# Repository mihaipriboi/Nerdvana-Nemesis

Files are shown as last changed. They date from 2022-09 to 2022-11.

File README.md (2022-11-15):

# Nerdvana Nemesis

### Team: Antonia Onisoru, Teodor Balan, Mihai Priboi
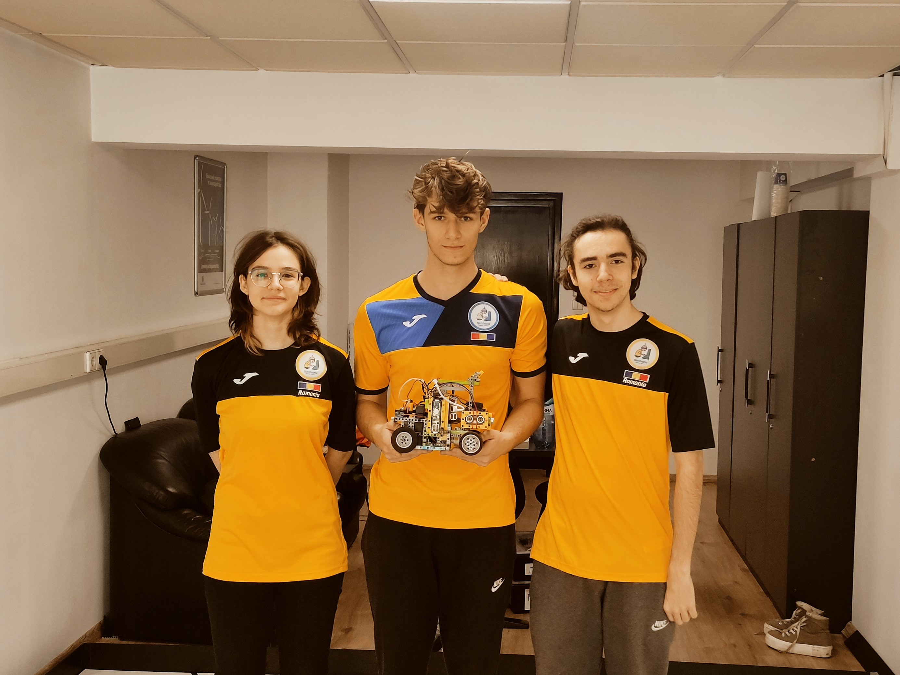
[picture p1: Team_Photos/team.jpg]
Team
  

## Our video of the robot on [Youtube](https://youtu.be/-w9J5_oPF1A)

## Repository content
  - The "Final" folder contains the final code for the final stage
  - The "Qualifing" folder contains the final code for the qualification stage
  - The "Electrical Diagram" folder contains a schematic of the electromechanical representation of the robot
  - The "3D_models" folder contains 3D models for printing the robot
  - The "Robot Photos" folder contains the robot photos required by the regulation
  - The "Team Photos" folder contains the team photos required by the regulation

## Introduction
  We have been participating at WRO for the last couple of years, but 2022 was the first year when, in our country, Romania, Future Engineers was held. When we first started thinking about how to build our robot, we realized that it was not going to be the same as we were used to. 
  
  It was clear to us that lego electronics weren't going to be good enough for what we wanted, so we decided to use Raspberry Pi and Arduino so we could use cameras and other sensors. Since the Arduino is better for sensors, but we could only use a Raspberry Pi for a camera, we decided to use both, in serial communication. As for connecting all the pieces, we still used lego pieces with 3D-printed parts for the non-lego components. In this way, we have a modular robot, easy to modify, so it was simple to try different mechanisms during the year. 

  For the national competition, we came up with the idea of using an Arduino to measure distances with 2 ultrasonic sensors, and a Raspberry pi to identify the cubes with a camera, and also control the drive and steering motors. We have constructed the robot so it has rear-wheel drive with frontal steering.
  
   After we qualified for the international, we started making some changes, such as trying to make the robot faster and more constant. So we added a gyroscope sensor, and an ultrasonic sensor in the front and made the robot smaller. Also, we upgraded from an Arduino Uno to an Arduino Nano Every, because it has more interrupt pins. In addition, we tried changing the drive motor to a micromotor in order to make it faster. Unfortunately, even though it made the robot much faster, we fried the ones we tested. We believe it happened because the robot was too heavy for the motor, causing it to overheat and eventually fry it.

## Photos our robot Paula (**P**retty **A**wesome **U**ltra **L**ow **A**ccurate robot)
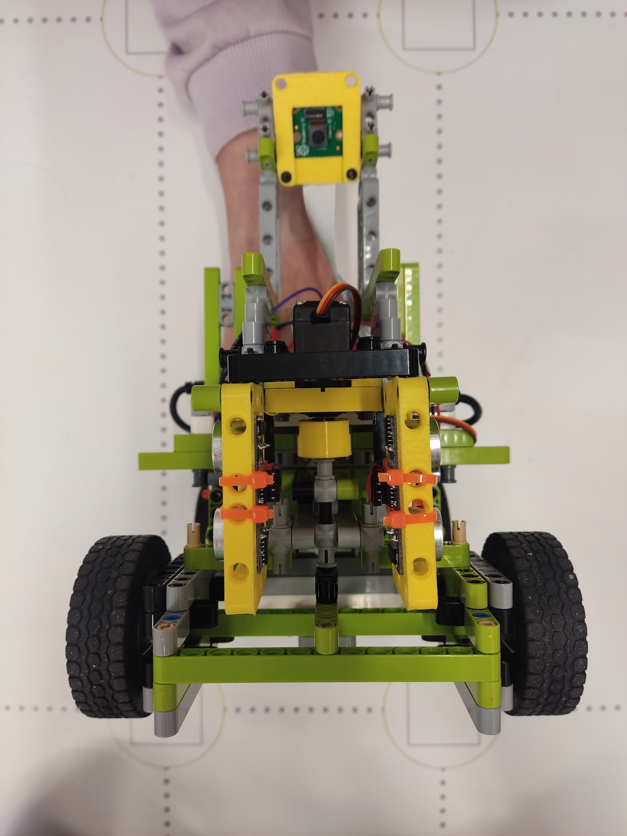
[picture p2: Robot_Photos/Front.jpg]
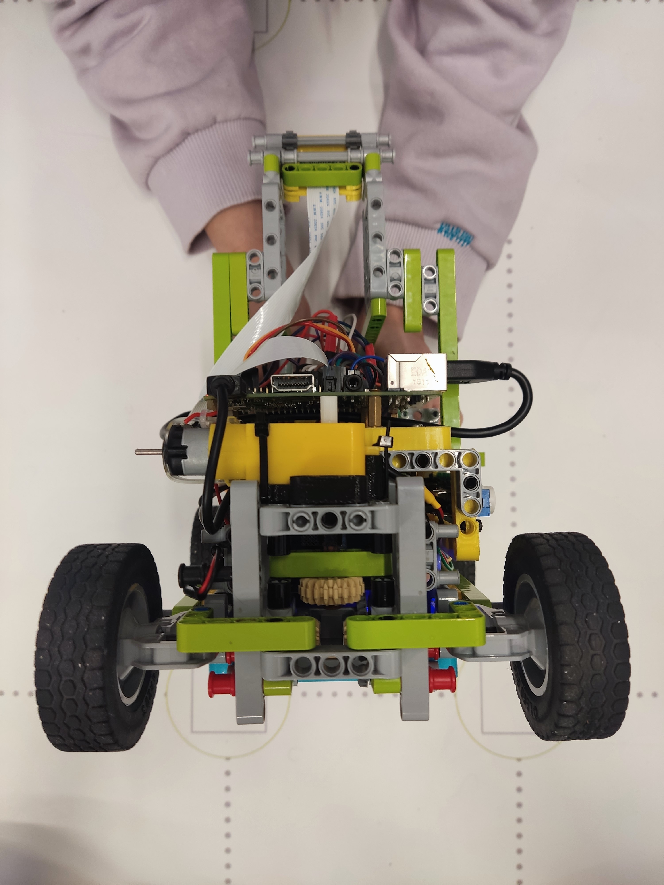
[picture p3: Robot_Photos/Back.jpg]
|  |  | 
| :--: | :--: |
| *Front* | *Back* |
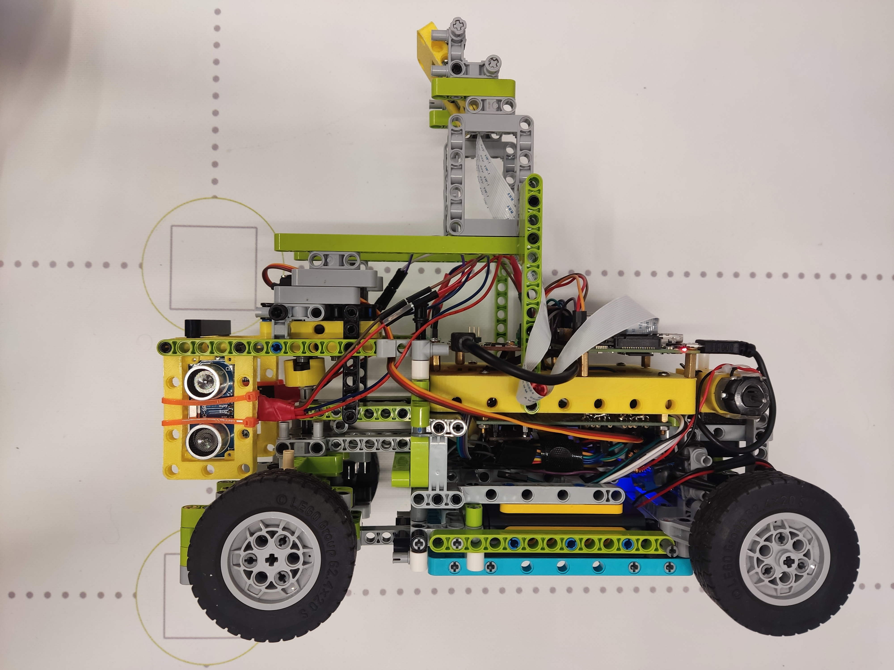
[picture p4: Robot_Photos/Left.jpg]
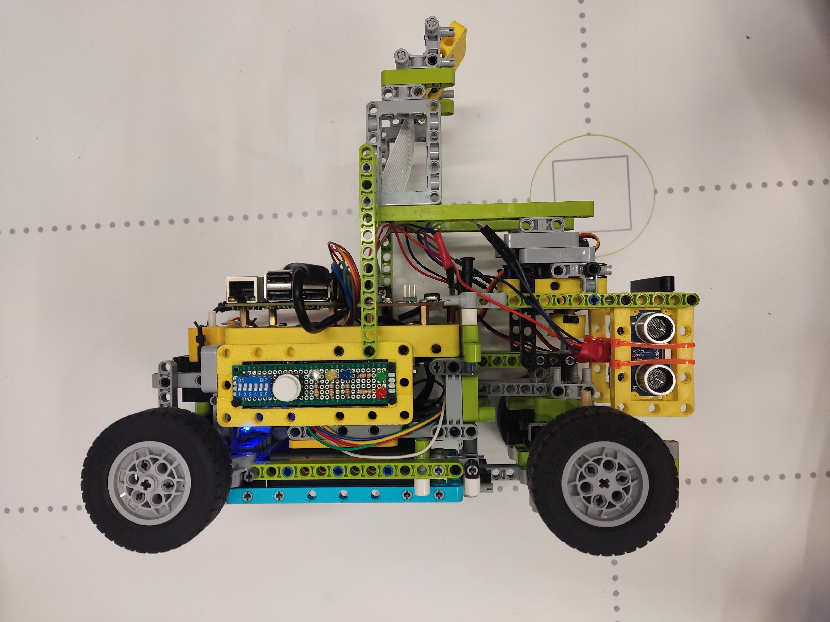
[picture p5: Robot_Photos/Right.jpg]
|  |  | 
| *Left* | *Right* |
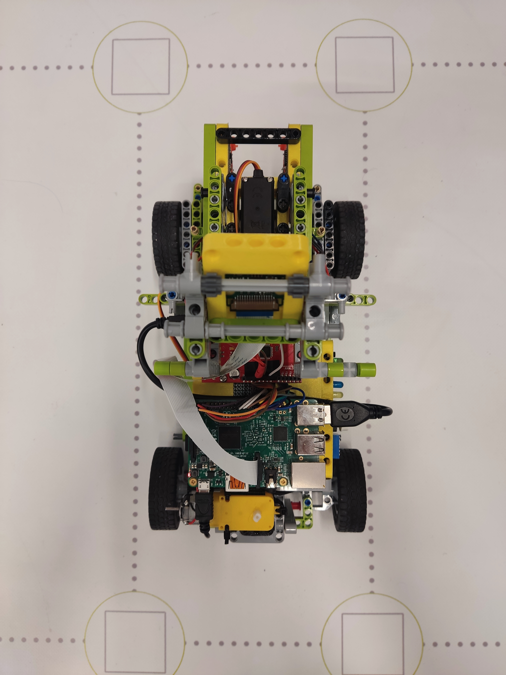
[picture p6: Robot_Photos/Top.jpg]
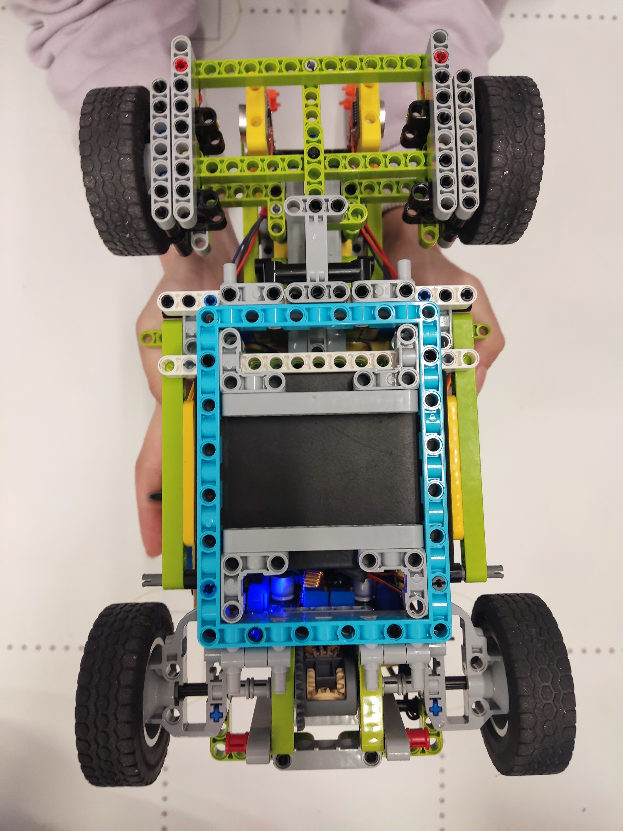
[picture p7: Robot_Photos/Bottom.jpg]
|  |  | 
| *Top* | *Bottom* |

## Electrical diagram
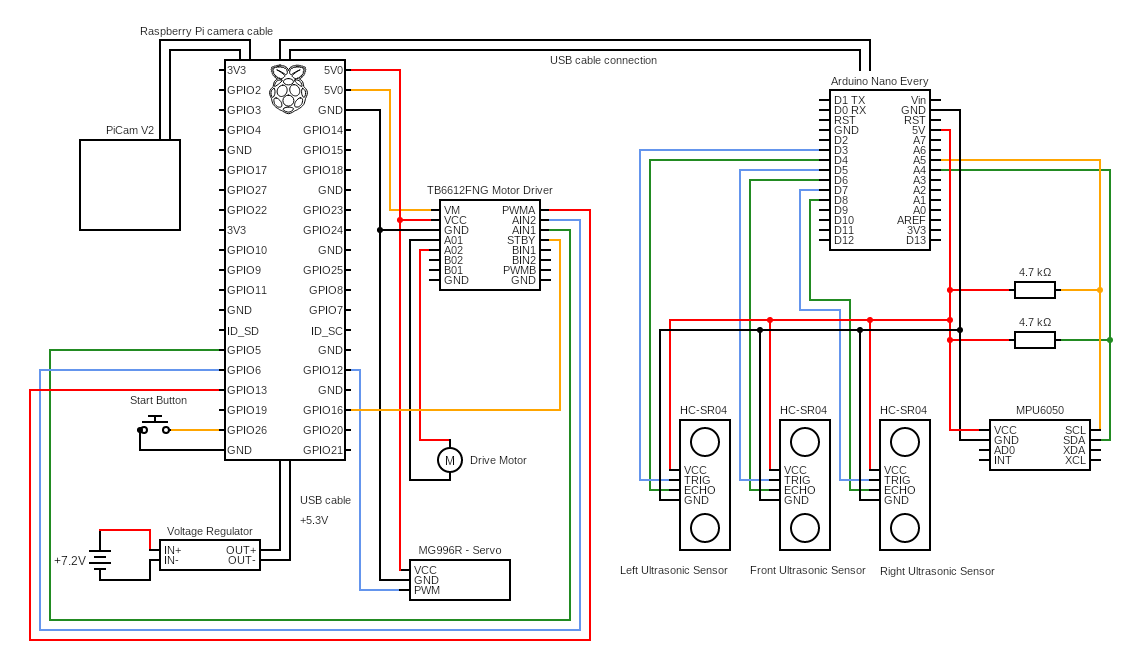
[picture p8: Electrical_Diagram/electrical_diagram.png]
Diagram
  

## Building the robot
  The structure of the robot is made out of lego pieces and 3D printed parts, which we designed. All the 3D printed parts are made to hold the electrical components that we couldn't mount with lego pieces.
  
  Since the battery pack is the heaviest part, we positioned it at the back of the robot to put as much force on the drive wheels. Everything is as low as possible to increase stability.
  
  The Raspberry Pi and the prototype PCB board are mounted on a bigger 3D printed part, positioned in the middle, used to connect the front and back of the robot. The Arduino is also zip tied on the same part. Additionally, in the middle, on the side, there is a "control board" with the start button and a few LEDs.
  
  As for the steering and differential systems, they are made out of lego pieces. The MPU6050 gyro sensor needs to be firmly secured, however its position on the robot is not important. In the front there are the 3 ultrasonic sensors facing left, front and right, and the servo motor, right above the steering system.
  
  Last but not least, the camera is placed high up in order to see as much as possible of the map, and to the front so it doesn't see other parts of the robot.

### The components we are currently using are:
  - Raspberry Pi 3B
  - Arduino Nano Every
  - SparkFun Motor Driver - Dual TB6612FNG
  - Hobby Gearmotor
  - MG966R Servo Motor
  - 3 x HC-SR04 Ultrasonic Sensors
  - MPU6050 Accelerometer and Gyroscope Sensor
  - PiCam V2
  - DC-DC Voltage Converter (To convert the 7.2V from the powersource to 5.3V for the Raspberry Pi)
  - 6 x AA 1.2V Acumulators

## Code for the components
### Motor driver
```python
import RPi.GPIO as GPIO

GPIO.setmode(GPIO.BOARD)
GPIO.setwarnings(False);

# Pin numbers
PWMA = 33
AIN1 = 29
AIN2 = 31
STBY = 36

# Pin setup
GPIO.setup(PWMA, GPIO.OUT)
GPIO.setup(AIN2, GPIO.OUT)
GPIO.setup(AIN1, GPIO.OUT)
GPIO.setup(STBY, GPIO.OUT)

# Initialisation
pwmFreq = 100
pwma = GPIO.PWM(PWMA, pwmFreq)
pwma.start(100)

# Functions
def motorStart(speed):
    GPIO.output(STBY, GPIO.HIGH);
    in1 = GPIO.HIGH
    in2 = GPIO.LOW

    if(speed < 0):
        speed = speed * -1
        in1 = GPIO.LOW
        in2 = GPIO.HIGH

    GPIO.output(AIN1, in1)
    GPIO.output(AIN2, in2)
    pwma.ChangeDutyCycle(speed)

def motorStop():
    GPIO.output(STBY, GPIO.LOW)
```
### Servo
```python
from gpiozero import Servo
from gpiozero.pins.pigpio import PiGPIOFactory

factory = PiGPIOFactory()

# Pin numbers
SERV = 12  # GPIO pin!

# Initialisation
servo = Servo(SERV, min_pulse_width=1.03/1000, max_pulse_width=1.97/1000, pin_factory=factory)

# Functions
def clamp(val, small, big):
    return max(small, min(val, big))

def moveServo(angle):
    servoCorrection = 0.04
    angle = clamp(angle, -1 + servoCorrection, 1 - servoCorrection)
    angle += servoCorrection
    servo.value = angle
```
### Camera
```python
import cv2
import numpy as np
from picamera.array import PiRGBArray
from picamera import PiCamera

IMAGE_WIDTH = 320
IMAGE_HEIGHT = 240

camera = PiCamera()
camera.resolution = (IMAGE_WIDTH, IMAGE_HEIGHT)
camera.framerate = 40

try:
    rawCapture = PiRGBArray(camera, size=(IMAGE_WIDTH, IMAGE_HEIGHT))

    for frame in camera.capture_continuous(rawCapture, format="bgr", use_video_port=True):
        image = frame.array
        img = imgProcc(image)
        cv2.imshow("Frame", img)

        key = cv2.waitKey(1) & 0xFF
        # clear the stream in preparation for the next frame
        rawCapture.truncate(0)
        # if the `q` key was pressed, break from the loop
        if key == ord("q"):
            break
```
### Arduino connection
```python
import serial
import time
from threading import Thread
import sys

arduino_read = ""
def arduinoReceving(ser):
    global arduino_read, endProgram
    while endProgram == False:
        if ser.in_waiting > 0:
            arduino_read = ser.readline().decode('utf-8', 'ignore').rstrip()
            arduino_read = arduino_read
            print("raw: " + arduino_read) 

def readSensors():
    global arduino_read
    sensor = arduino_read.split()
    if len(sensor) > 1:
        return (int(sensor[0]), int(sensor[1]), int(sensor[2]), float(sensor[3]))
    else:
        return (0, 0, 0, 0)
    
def startSerial(tries):
    ser = serial.Serial('/dev/ttyACM0', 115200, timeout=1)
    time.sleep(0.1)
    ser.reset_input_buffer()
    time.sleep(0.1)
    ser.write(b"\n")
    time.sleep(0.1)
    if ser.in_waiting > 0:
        tries += 1
        if tries == 2:
            return ser
    
    ser.close()
    print("Serial communcation failed!")
    return startSerial(tries)

try:
    ser = startSerial(0)
    print("Serial communcation ok!")
    Thread(target=arduinoReceving, args=(ser,)).start()
    time.sleep(3.5)
```
### Ultrasonic
```ino
#include "HC_SR04.h"

#define TRIG_PIN 3
#define ECHO_PIN 4

HC_SR04 sensor(TRIG_PIN, ECHO_PIN, digitalPinToInterrupt(ECHO_PIN));

long startTime, interval = 75;

void setup() {
  Serial.begin(115200);

  while(Serial.available() == 0);

  delay(10);
  Serial.println("ok!");

  sensor.begin();
  sensor.start();
  startTime = millis();
}

void loop() {
  if(millis() - startTime > interval) {
    if(sensor.isFinished()) {
      Serial.println(sensorLeft.getRange());
      sensor.start();
    }
    startTime = millis();
  }
}
```
### MPU6050 Gyro
```ino
#include <MPU6050_tockn.h>
#include <Wire.h>

MPU6050 mpu6050(Wire);

long startTime, interval = 75;

void setup() {
  Serial.begin(115200);

  while(Serial.available() == 0);

  delay(10);
  
  Wire.begin();
  Wire.setTimeout(true);
  
  mpu6050.begin();
  Serial.println("ok!");
  mpu6050.calcGyroOffsets(false);

  //mpu6050.setGyroOffsets(-34, 2.17, 0.63);
  
  Serial.println("ok!");
  
  startTime = millis();
}

void loop() {
  mpu6050.update();
  
  if(millis() - startTime > interval) {
    Serial.println(mpu6050.getGyroAngleX());
    startTime = millis();
  }
}
```

## How to run our code
  - To program the robot you need to connect to the Raspberry pi either with a monitor or capture card using a HDMI cable or Wirelessly using VNC Viewer, a computer app we used so we could work without the bother of a cable.
  - The first step to running the code is to set up and install all the libraries necessary for the camera, image processing, and serial communication by using the Rasberry Pi terminal. To do that you must follow the instructions below: 
    - Open the terminal and update the Raspberry Pi OS by typing the following line:
    ```
    sudo apt-get update
    sudo apt-get upgrade
    ```
    - Then, after you finished updating the Raspberry Pi OS, open the configurations by running the following  commands:
    ```
    sudo raspi-config
    ```
    - Now, in the interfacing options, you need to enable the Camera and I2C.
    - After, enabling the Camera and I2C, we go back to installing libraries. Open the terminal again and type the commands below:
    ```
    sudo apt-get install python3-pip
    sudo pip-3.2 install picamera
    sudo pip-3.2 install picamera
    sudo apt-get install libopencv-dev
    sudo apt-get install libatlas-base-dev
    sudo pip3 install virtualenv Pillow numpy scipy matplotlib
    sudo pip3 install opencv-python opencv-contrib-python
    sudo apt-get install python-serial
    sudo pip3 install gpiozero
    sudo apt-get install rpi.gpio
    ```
    - Last but not least, you need to reboot the Rasberry Pi.
  - In addition,  you can install the Arduino IDE on the Rasberry Pi, so you can upload the C++ code easier. Therefore, you don't have to switch between the two boards to run and change the C++ code, if you need to. Also, the IDE has a friendly user interface and it's well documented on the internet.
  - Now that everything is installed you should be able to run the main program on the Raspberry Pi. So all that is left for you to do is to open the terminal, go into the folder in which the program is located, and execute the .py file. You can do that with commands such as:
  ```
  cd "folder"
  python "file".py
  ```
  -  While the Arduino starts the program by itself when it is powered on, the Raspberry Python code has to be set to start up on power on

## Starting the robot
 - Turn on the robot with the switch on the battery pack
 - Place the robot on the track
 - Wait for about 8 seconds for the gyro to stabilize and camera to start
 - Press the start button

## Our future plans
  With our failed attempt to change the drive motor for a higher speed, that is one of our most important future task. We hope that by trying to use a bigger motor, or even better, making the robot smaller and lighter, we can increase our speed.
  
  The Raspberry Pi is great for what it was designed for: being a small computer. But, for this task, what is needed is speed and accuracy, and a microcontroller is all we need. We used a Raspberry Pi to process what the camera sees, and an Arduino for the sensors. However, good communication between the two is difficult and problematic. Fortunately, we found some camera modules that include processing, which could be directly read by a microcontroller like Arduino, so we wouldn't need a Raspberry Pi. We hope to test this solution as soon as possible because we believe that running everything on a single board (preferably a very fast one), will increase the accuracy of the data we process and the movement that the robot makes. Moreover, even if it isn't a big deal, programming would be easier, changing the code on only the microcontroller, and not having to connect to the Raspberry Pi.
  
  Making the robot smaller is also important. It means higher speed, easier maneuvering, and much better efficiency in general. That being said, we believe that made out of legos, it is very close to being as small as possible, so we plan to design almost all of it and 3D print it. It has always been a plan for us, but we needed to be sure that the layout for everything is optimal.

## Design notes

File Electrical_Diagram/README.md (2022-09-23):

# Electrical Diagram
The diagram was made using www.circuit-diagram.org

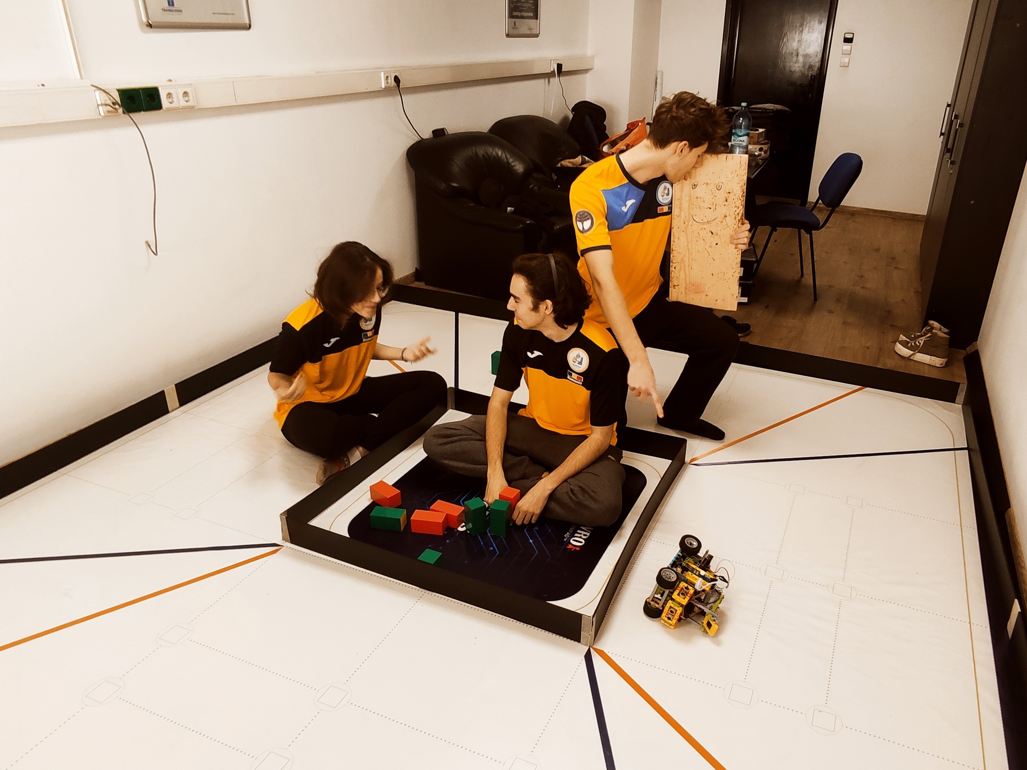
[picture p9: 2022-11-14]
Team_Photos/funny.jpg

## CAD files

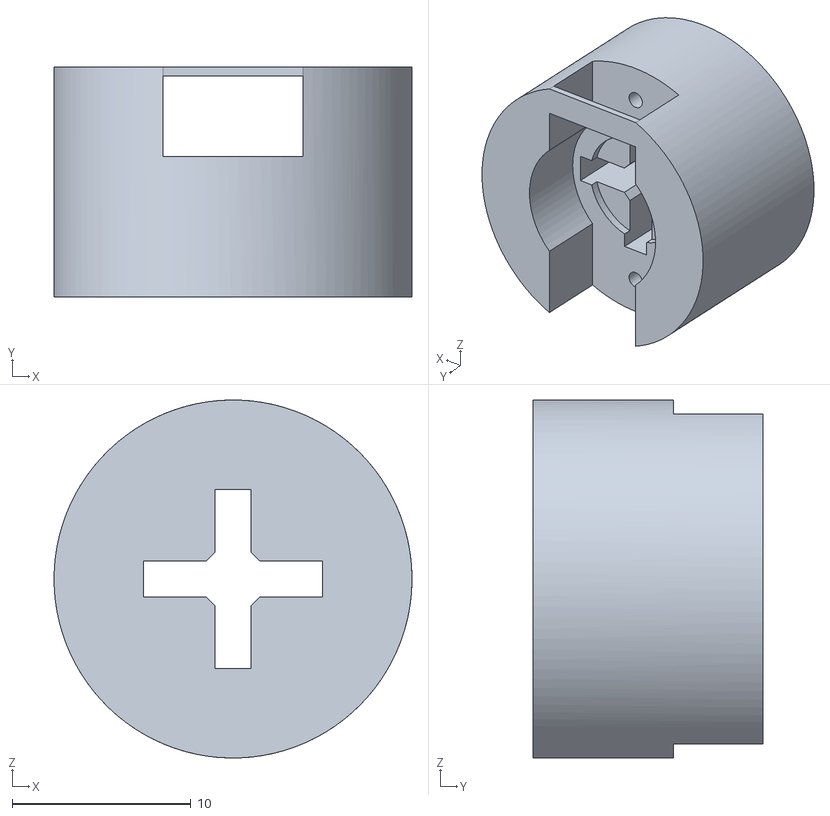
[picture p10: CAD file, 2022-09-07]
3D_models/MG996R_to_axle.stl
20.0 x 12.9 x 20.0

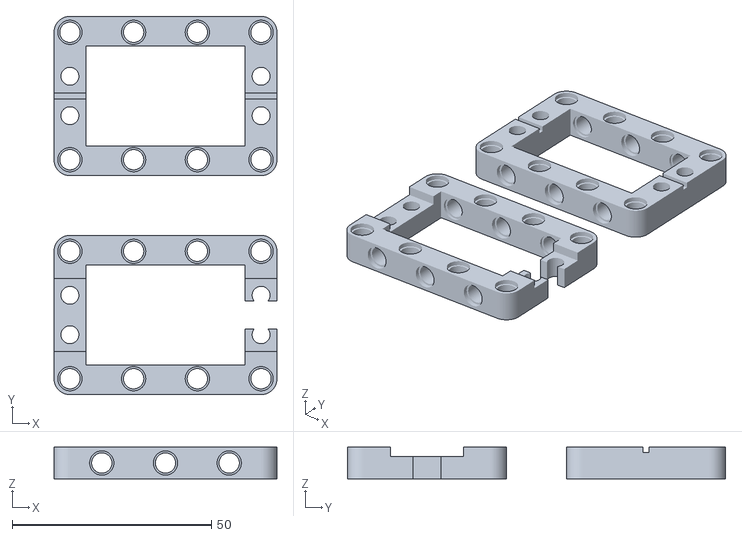
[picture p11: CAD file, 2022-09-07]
3D_models/MG996R.stl
56.0 x 95.0 x 8.00

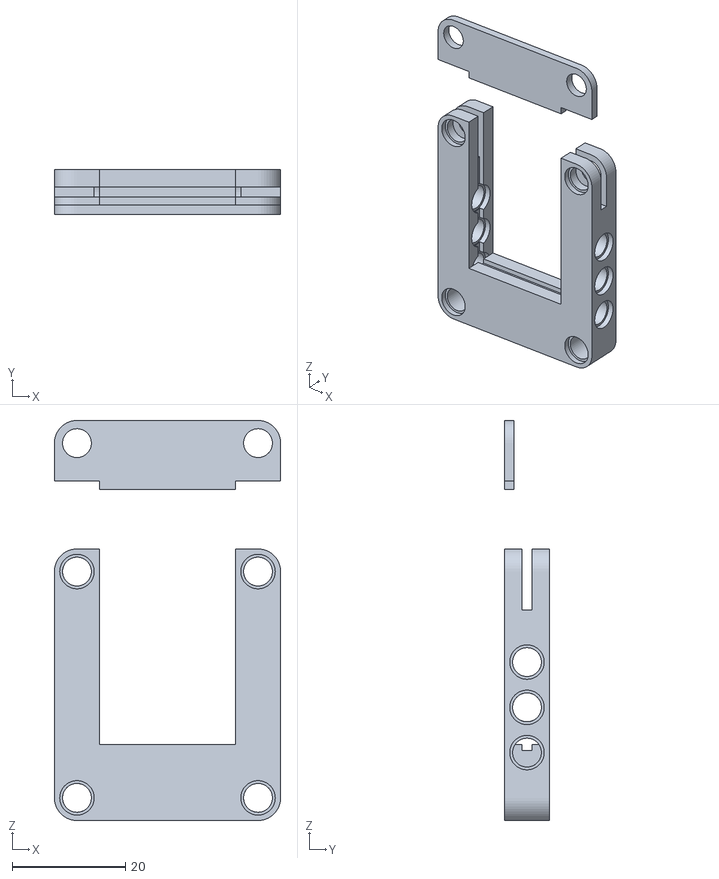
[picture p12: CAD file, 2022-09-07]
3D_models/picamv2.stl
40.0 x 8.00 x 70.7

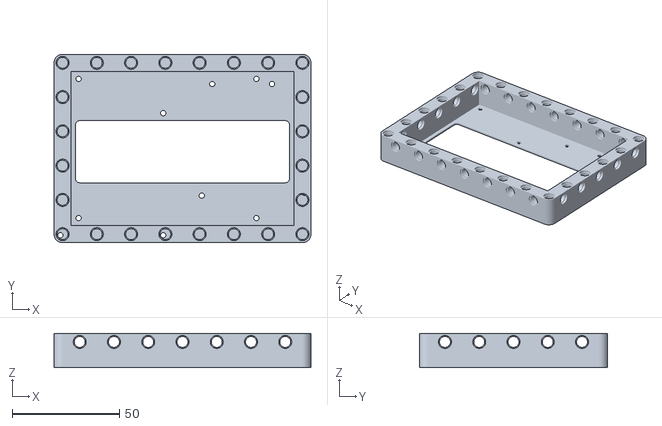
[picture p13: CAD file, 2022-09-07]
3D_models/raspi_arduino.stl
120.0 x 88.0 x 16.0

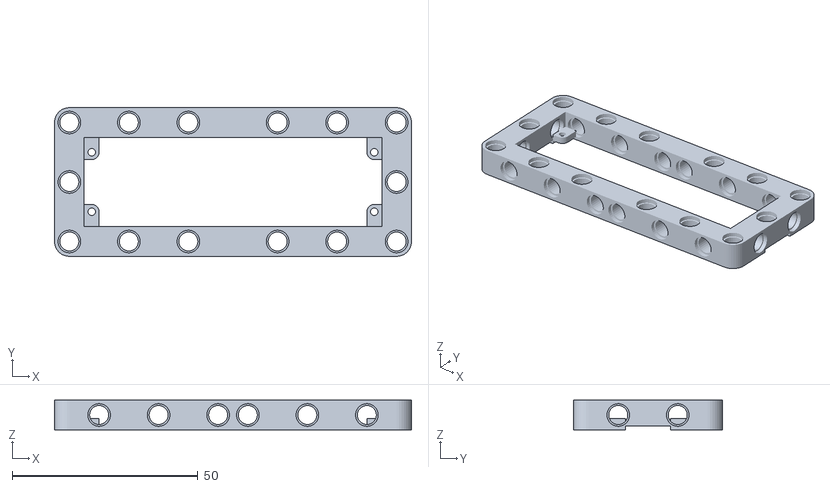
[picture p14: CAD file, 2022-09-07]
3D_models/control_board.stl
96.0 x 40.0 x 8.00

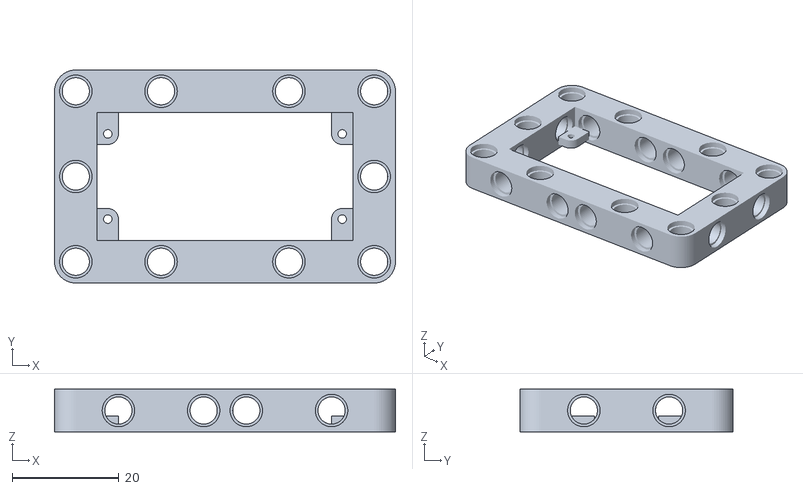
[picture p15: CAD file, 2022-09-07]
3D_models/ultrasonic.stl
64.0 x 40.0 x 8.00

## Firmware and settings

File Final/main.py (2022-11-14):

import math
import serial
import time
from gpiozero import Servo
from gpiozero import Button
from gpiozero.pins.pigpio import PiGPIOFactory
import RPi.GPIO as GPIO
from threading import Thread
import sys
import cv2
import numpy as np
from picamera.array import PiRGBArray
from picamera import PiCamera


#############################################
#        Defines and Initializations        #
#############################################

################### Board ###################

GPIO.setmode(GPIO.BOARD)
GPIO.setwarnings(False)

factory = PiGPIOFactory()

################ Pin numbers ################

# Start button
BUTTON = 26

# Motor driver
PWMA = 33
AIN1 = 29
AIN2 = 31
STBY = 36

# Servo motor
SERV = 12  # GPIO pin!!!

################ Setup Pins #################

GPIO.setup(BUTTON, GPIO.IN, pull_up_down=GPIO.PUD_UP)

# Motor driver
GPIO.setup(PWMA, GPIO.OUT)
GPIO.setup(AIN2, GPIO.OUT)
GPIO.setup(AIN1, GPIO.OUT)
GPIO.setup(STBY, GPIO.OUT)

############## Initialization ###############

button = Button(BUTTON)
servo = Servo(SERV, min_pulse_width=1.03/1000, max_pulse_width=1.97/1000, pin_factory=factory)

# Motor driver
pwmFreq = 100
pwma = GPIO.PWM(PWMA, pwmFreq)
pwma.start(100)

#############################################
#                 Functions                 #
#############################################

############# Image Processing ##############

cubeColor = 0
cubeX = 0
cubeY = 0
def imgProcc(frame):
    global cubeColor, cubeX, cubeY
    img = cv2.blur(frame,(3,3))
    # show the frame
    hsv = cv2.cvtColor(img, cv2.COLOR_BGR2HSV)
    # lower bound and upper bound for Green color
    lower_boundGreen = np.array([50, 75, 15])  
    upper_boundGreen = np.array([95, 255, 255])
    # find the colors within the boundaries
    maskGreen = cv2.inRange(hsv, lower_boundGreen, upper_boundGreen)
    
    #red
    lower1 = np.array([0, 100, 20])
    upper1 = np.array([5, 255, 255])
     
    # upper boundary RED color range values; Hue (160 - 180)
    lower2 = np.array([160,100,20])
    upper2 = np.array([182,255,255])
     
    lower_mask = cv2.inRange(hsv, lower1, upper1)
    upper_mask = cv2.inRange(hsv, lower2, upper2)
     
    maskRed = lower_mask + upper_mask;
    
    
    kernel = np.ones((7,7),np.uint8)
    # Remove unnecessary noise from mask
    maskGreen = cv2.morphologyEx(maskGreen, cv2.MORPH_CLOSE, kernel)
    maskGreen = cv2.morphologyEx(maskGreen, cv2.MORPH_OPEN, kernel)
    maskRed = cv2.morphologyEx(maskRed, cv2.MORPH_CLOSE, kernel)
    maskRed = cv2.morphologyEx(maskRed, cv2.MORPH_OPEN, kernel)
    
    contoursGreen, hierarchy = cv2.findContours(maskGreen, cv2.RETR_EXTERNAL, cv2.CHAIN_APPROX_SIMPLE)
    contoursRed, hierarchy = cv2.findContours(maskRed, cv2.RETR_EXTERNAL, cv2.CHAIN_APPROX_SIMPLE)
    img = cv2.drawContours(img, contoursRed, -1, (0, 0, 255), 3)
    img = cv2.drawContours(img, contoursGreen, -1, (0, 255, 0), 3)
    minArea = 150
    
    cubeColor = ''
    maxArea = minArea
    
    for green in contoursGreen:
        areaGreen = cv2.contourArea(green)
        if areaGreen > minArea:
            cubeColor = 'G'
            if maxArea < areaGreen:
                maxArea = areaGreen
            M = cv2.moments(green)
            cx,cy = int(M['m10']/M['m00']), int(M['m01']/M['m00'])
            cubeX, cubeY = cx, cy
            #print("Coords x and y for green: ", cx, cy)
            cv2.circle(img,(cx,cy),5,(0,255,0),-1)
    for red in contoursRed:
        areaRed = cv2.contourArea(red)
        if areaRed > minArea:
            if maxArea < areaRed:
                maxArea = areaRed
                cubeColor = 'R'
            M = cv2.moments(red)
            cx,cy = int(M['m10']/M['m00']), int(M['m01']/M['m00'])
            cubeX, cubeY = cx, cy
            #print("Coords x and y for red: ", cx, cy)
            cv2.circle(img,(cx,cy),5,(255,0,0),-1)
    
    return img

def getCubeColor(currentSide, turnDir):
    global cubeColor, cubeX, cubeY
    sideDist = 10
    
    cube = ''
    if currentSide == 0:
        if sideDist < cubeX and cubeX < IMAGE_WIDTH - sideDist:
            cube = cubeColor
        if 50 < cubeY:
            cube = cubeColor
    elif currentSide == -1 and turnDir == -1:
        if IMAGE_WIDTH / 2 < cubeX:
            cube = cubeColor
    elif currentSide == 1 and turnDir == 1:
        if IMAGE_WIDTH / 2 > cubeX:
            cube = cubeColor
    else:
        cube = cubeColor
        
    #print(cubeX, cubeY, cubeColor)
    return cube

################ Drive Motor ################

def motorStart(speed):
    GPIO.output(STBY, GPIO.HIGH);
    in1 = GPIO.HIGH
    in2 = GPIO.LOW

    if(speed < 0):
        speed = speed * -1
        in1 = GPIO.LOW
        in2 = GPIO.HIGH

    GPIO.output(AIN1, in1)
    GPIO.output(AIN2, in2)
    pwma.ChangeDutyCycle(speed)

def motorStop():
    GPIO.output(STBY, GPIO.LOW)

############ Arduino Connection #############

arduino_read = ""
def arduinoReceving(ser):
    global arduino_read, endProgram
    while endProgram == False:
        if ser.in_waiting > 0:
            arduino_read = ser.readline().decode('utf-8', 'ignore').rstrip()
            arduino_read = arduino_read
            print("raw: " + arduino_read) 

def readSensors():
    global arduino_read
    sensor = arduino_read.split()
    if len(sensor) > 1:
        return (int(sensor[0]), int(sensor[1]), int(sensor[2]), float(sensor[3]))
    else:
        return (0, 0, 0, 0)
    
def startSerial(tries):
    ser = serial.Serial('/dev/ttyACM0', 115200, timeout=1)
    time.sleep(0.1)
    ser.reset_input_buffer()
    time.sleep(0.1)
    ser.write(b"\n")
    time.sleep(0.1)
    if ser.in_waiting > 0:
        tries += 1
        if tries == 2:
            return ser
    
    ser.close()
    print("Serial communcation failed!")
    return startSerial(tries)

################ Servo Motor ################

def clamp(val, small, big):
    return max(small, min(val, big))

def moveServo(angle):
    servoCorrection = 0.04
    angle = clamp(angle, -1 + servoCorrection, 1 - servoCorrection)
    angle += servoCorrection
    servo.value = angle

############## Move Functions ###############
    
def sMove(startSide, finishSide):
    global servo, currentSide
    # -1 -> left; 0 -> center; 1 -> right
    if startSide != finishSide: 
        moveServo(finishSide)
        time.sleep(0.85 + abs(startSide) * 0.25)
        moveServo(-finishSide)
        time.sleep(0.88 + abs(startSide) * 0.25)
        moveServo(0)
        currentSide = finishSide

def driveToDist(dist):
    global centerAngle, turnDirection
    
    lastError = 0
    integral = 0
    
    (leftSensor, frontSensor, rightSensor, gyro) = readSensors()
    while (leftSensor + rightSensor) < 100:
        (leftSensor, frontSensor, rightSensor, gyro) = readSensors()
        #print(frontSensor, leftSensor, rightSensor)
        
        error = centerAngle - gyro
        angle = kP * error + kD * (error - lastError)
        lastError = error
        moveServo(angle)
        
    driveTime(1, 0.1)
    
    while frontSensor > dist:
        (leftSensor, frontSensor, rightSensor, gyro) = readSensors()
        #print(frontSensor, leftSensor, rightSensor)
        
        error = centerAngle - gyro
        angle = kP * error + kD * (error - lastError)
        lastError = error
        moveServo(angle)
    
    if turnDirection == 0 and (leftSensor + rightSensor) > 110:
        if leftSensor > rightSensor:
            turnDirection = -1
        else:
            turnDirection = 1
        
def driveToTurn():
    driveToDist(90)

def driveToCube():
    lastError = 0
    integral = 0
    
    frontSensor = 400
    while cubeColor == '':
        (leftSensor, frontSensor, rightSensor, gyro) = readSensors()
        
        error = centerAngle - gyro
        angle = kP * error + kD * (error - lastError)
        lastError = error
        moveServo(angle)
        
def driveTime(direction, wait):
    lastError = 0
    integral = 0
    startTime = time.time()
    
    (leftSensor, frontSensor, rightSensor, gyro) = readSensors()
    while time.time() - startTime < wait:
        (leftSensor, frontSensor, rightSensor, gyro) = readSensors()
        
        error = (centerAngle - gyro) * direction
        angle = kP * error + kD * (error - lastError)
        lastError = error
        moveServo(angle)
        
def driveTimeFront(direction, wait):
    lastError = 0
    integral = 0
    startTime = time.time()
    
    (leftSensor, frontSensor, rightSensor, gyro) = readSensors()
    while time.time() - startTime < wait:
        (leftSensor, frontSensor, rightSensor, gyro) = readSensors()
        
        error = (centerAngle - gyro) * direction
        angle = kP * error + kD * (error - lastError)
        lastError = error
        moveServo(angle)

################### Turns ###################

def extTurn(turnDir):
    global centerAngle
    
    driveTime(1, 0.58)
    
    # Turn 90 degrees in the direction of the circuit
    centerAngle += real90Deg * turnDir
    
    (leftSensor, frontSensor, rightSensor, gyro) = readSensors() 
    while (centerAngle - gyro) * turnDir > 14:
        (leftSensor, frontSensor, rightSensor, gyro) = readSensors()
        moveServo(turnDir)
    
    moveServo(0)
    
    # Go backwards to have space for S move
    motorStop()
    time.sleep(0.5)
    motorStart(-80)
    driveTime(-1, 0.35)
    motorStop()
    time.sleep(0.5)
    
    
def centTurn(turnDir):
    global centerAngle
    
    driveTime(1, 0.55)
    
    # Turn 90 degrees in the direction of the circuit
    centerAngle += real90Deg * turnDir
    
    (leftSensor, frontSensor, rightSensor, gyro) = readSensors()
    while (centerAngle - gyro) * turnDir > 14:
        (leftSensor, frontSensor, rightSensor, gyro) = readSensors()
        moveServo(turnDir)
    
    moveServo(0)
    
    # Go backwards to have space for S move
    motorStop()
    time.sleep(0.5)
    motorStart(-80)
    driveTime(-1, 0.7)
    motorStop()
    time.sleep(0.5)
    
def intTurn(turnDir):
    global centerAngle
    
    # Stop near the wall
    driveToDist(15)
    time.sleep(0.03)
    motorStop()
    time.sleep(0.5)
    
    # Turn backwards, as to not hit the cube
    motorStart(-speed)
    
    centerAngle += real90Deg * turnDir
    
    (leftSensor, frontSensor, rightSensor, gyro) = readSensors()
    while (centerAngle - gyro) * turnDir > 9:
        (leftSensor, frontSensor, rightSensor, gyro) = readSensors()
        moveServo(-turnDir)
    
    moveServo(0)
    motorStop()
    time.sleep(0.1)
    
    motorStart(-speed)
    driveTime(-1, 0.7)
    motorStop()
    time.sleep(0.5)

################ Main Thread ################

def laps():
    global turnDirection, cubeColor, currentSide, centerAngle, endProgram
    
    # Variables
    turnDirection = 0
    currentSide = 0
    
    # Program loop start
    moveServo(0)
    time.sleep(3)
    
    
    button.wait_for_press()
    print("Run started!")
    runStartTime = time.time()
    
    (leftSensor, frontSensor, rightSensor, centerAngle) = readSensors()
    
    #centerAngle -= 0.3
    
    #while True: getCubeColor(0, turnDirection)
    
    for i in range(12):
        motorStart(speed)
        print("cube color 1: ", end='')
        print(getCubeColor(currentSide, turnDirection))
        
        if getCubeColor(currentSide, turnDirection) == 'R':
            sMove(currentSide, 1)
        elif getCubeColor(currentSide, turnDirection) == 'G':
            sMove(currentSide, -1)
            
        #driveTime(1, 0.3)
        
        driveToTurn()
        
        if currentSide * turnDirection == 1:
            intTurn(turnDirection)
        elif currentSide == 0:
            centTurn(turnDirection)
        else:
            extTurn(turnDirection)
        
        currentSide = 0
        
        motorStart(speed)
        driveToCube()
        
        print("cube color 2: ", end='')
        print(getCubeColor(currentSide, turnDirection))
        
        if getCubeColor(currentSide, turnDirection) == 'R':
            sMove(currentSide, 1)
            driveTime(1, 0.8)
        elif getCubeColor(currentSide, turnDirection) == 'G':
            sMove(currentSide, -1)
            driveTime(1, 0.8)
        
        motorStop()
        time.sleep(0.2)
        
        print("Lap " + str(i) + " done!")
        
    motorStart(speed)
    driveTime(1, 0.8)
    motorStop()
    time.sleep(1)
    
    print("Run has ended in: " + str(time.time() - runStartTime))
    
    endProgram = True

#############################################
#                   Main                    #
#############################################

    
if __name__ == "__main__":
    IMAGE_WIDTH = 320
    IMAGE_HEIGHT = 240
    
    camera = PiCamera()
    camera.resolution = (IMAGE_WIDTH, IMAGE_HEIGHT)
    camera.framerate = 40
    
    speed = 100
    
    kP = 0.038 
    kI = 0
    kD = 0.19
    offset = 0
    
    real90Deg = 84.25
    
    endProgram = False
    
    try:
        motorStop()
        moveServo(0)
        
        ser = startSerial(0)
        
        print("Serial communcation ok!")
        Thread(target=arduinoReceving, args=(ser,)).start()
        time.sleep(3.5)
        
        rawCapture = PiRGBArray(camera, size=(IMAGE_WIDTH, IMAGE_HEIGHT))
        time.sleep(1)
        Thread(target=laps).start()
        
        print("Program Start")
        
        for frame in camera.capture_continuous(rawCapture, format="bgr", use_video_port=True):
            image = frame.array
            img = imgProcc(image)
            cv2.imshow("Frame", img)
            
            key = cv2.waitKey(1) & 0xFF
            # clear the stream in preparation for the next frame
            rawCapture.truncate(0)
            # if the `q` key was pressed, break from the loop
            if key == ord("q"):
                break
        
        
    finally:
        endProgram = True
        moveServo(0)
        motorStop()
        GPIO.cleanup()
        time.sleep(1)
        sys.exit()
        print("Program has ended")

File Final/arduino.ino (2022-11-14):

#include <MPU6050_tockn.h>
#include <Wire.h>
#include "HC_SR04.h"

#define TRIG_PIN1 3
#define ECHO_PIN1 4
#define TRIG_PIN2 5
#define ECHO_PIN2 6
#define TRIG_PIN3 7
#define ECHO_PIN3 8

HC_SR04_1 sensorLeft(TRIG_PIN1, ECHO_PIN1, digitalPinToInterrupt(ECHO_PIN1));
HC_SR04_2 sensorFront(TRIG_PIN2, ECHO_PIN2, digitalPinToInterrupt(ECHO_PIN2));
HC_SR04_3 sensorRight(TRIG_PIN3, ECHO_PIN3, digitalPinToInterrupt(ECHO_PIN3));

MPU6050 mpu6050(Wire);

int leftS = 0, frontS = 0, rightS = 0;
long startTime, interval = 75;

void setup() {
  Serial.begin(115200);

  while(Serial.available() == 0);

  delay(10);
  
  Wire.begin();
  Wire.setTimeout(true);
  
  mpu6050.begin();
  Serial.println("ok!");
  mpu6050.calcGyroOffsets(false);

  //mpu6050.setGyroOffsets(-34, 2.17, 0.63);

  sensorLeft.begin();
  sensorFront.begin();
  sensorRight.begin();

  sensorLeft.start();
  sensorFront.start();
  sensorRight.start();
  startTime = millis();
}

void loop() {
  mpu6050.update();
  
  if(millis() - startTime > interval) {
    if(sensorLeft.isFinished()) {
      leftS = sensorLeft.getRange();
      sensorLeft.start();
    }
    if(sensorFront.isFinished()) {
      frontS = sensorFront.getRange();
      sensorFront.start();
    }
    if(sensorRight.isFinished()) {
      rightS = sensorRight.getRange();
      sensorRight.start();
    }
    
    Serial.print(leftS);
    Serial.print(" ");
    Serial.print(frontS);
    Serial.print(" ");
    Serial.print(rightS);
    Serial.print(" ");
    Serial.print(mpu6050.getGyroAngleX());
    Serial.println();
    startTime = millis();
  }
}
